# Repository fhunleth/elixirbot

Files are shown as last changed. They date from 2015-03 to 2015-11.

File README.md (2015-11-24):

# ElixirBot

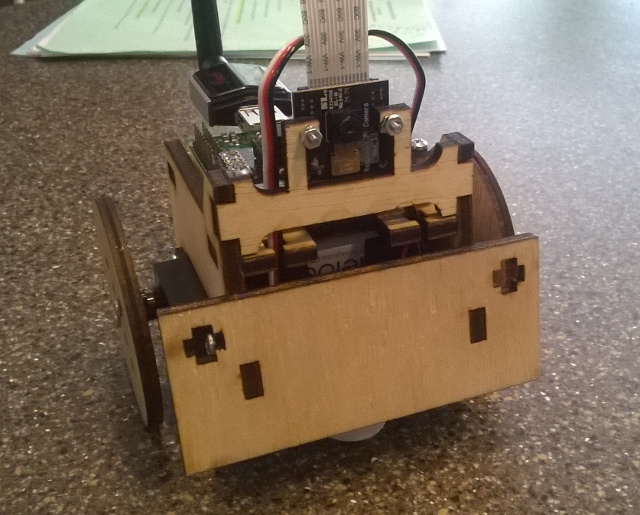
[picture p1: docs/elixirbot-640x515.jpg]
ElixirBot!!!


## Parts

The following lists all of the parts except for the laser cut frame and 3D
printed ball bearing holder. If you have a local hackerspace or Fab Lab, you're
in luck. If not, companies like Pololu and Ponoko will do it for you, but I have
not tested the designs with either of them.

  - Raspberry Pi Model A+ - $20
  - Pi Camera - $30
  - 2 [Spring RC SM-S4303R Servos](https://www.pololu.com/product/1248) - $26
  - WiFi dongle
  - [Daughter board PCB](https://oshpark.com/shared_projects/lCHfJqx6) - $3
  - [Pololu 5V Step-Up/Step-Down Voltage Regulator S7V7F5](https://www.pololu.com/product/2119) - $5
  - [4-AA Battery Holder](https://www.pololu.com/product/1153) - $1
  - [8-pin DIP socket](http://www.digikey.com/product-detail/en/A08-LC-TT/AE9986-ND/821740)
  - [10 position socket](http://www.digikey.com/product-detail/en/61301021821/732-2861-ND/2508630)
  - [2 position, 2.54 mm terminal block](http://www.digikey.com/product-detail/en/OSTVN02A150/ED10561-ND/1588862)
  - [ATtiny85](http://www.digikey.com/product-detail/en/ATTINY85-20PU/ATTINY85-20PU-ND/735469) - $2
  - [16 mm ball bearing](http://www.mcmaster.com/#9292k53/=w80vpw) - $1
  - [3/8" #6 pan head screws](http://www.mcmaster.com/#90190a146/=w80x6q)
  - [3/8" #4 pan head screws](http://www.mcmaster.com/#90190a103/=w80y2f)
  - [7/16" 4-40 F-F standoffs](https://www.pololu.com/category/114/female-female-standoffs)
  - [5/16" 4-40 machine screws](https://www.pololu.com/product/1961)
  - [4-40 machine hex nuts](https://www.pololu.com/product/1068)
  - [2-56 machine hex nuts](https://www.pololu.com/product/1067)
  - [5/16" 2-56 machine screws](https://www.pololu.com/product/1956)
  - [.1" header header]()
  - [.1" short]()
  - [10K resister 0805 package]()
  - [.1 uF capacitor 0805 package]()
  - MicroSD card
  - Rechargable AA batteries - Eneloop or other ~2000 mAh batteries

Very useful items:

  - [3V FTDI cable](https://www.sparkfun.com/products/9717)

## Building the frame

The robot frame is a modification of the awesome [SumoBot
Jr.](http://sumobotkit.com). I've made the following modifications to the
original design:

  1. Changed screw hole locations to mount a Raspberry Pi Model A
  2. Added a mount for a Pi Camera up front
  3. Added more room for batteries and enlarged the servo hole slightly
  4. Modified the wheels to screw into the servo horn rather than directly
     attaching (not completely sure that this is an improvement)

The `dxf` containing the laser cutter pattern was created in
[QCad](http://qcad.org). I cut the pattern in 5 mm birch plywood using a Full
Spectrum laser cutter. The Full Spectrum driver isn't smart about which lines to cut
first like the Epilog and Universal Laser drivers, so it has the cuts divided
into "first" and "second" passes.

## Building the electronics

First, order a PCB from [OSH Park](https://oshpark.com/shared_projects/lCHfJqx6).

IMPORTANT: I messed up the drill size for the 4-40 mounts, so the mounting holes
on the daughterboard need to be manually enlarged with a 7/64" drill bit. Don't
worry, I left clearance.

Solder the surface mount parts first. For the 10K resisters, make sure that you
have the orientation correct (same direction as silkscreen label). You'll see
what I mean.

The remaining components are fairly straightforward to solder since they're
through-hole. I didn't solder in the ISP connector, since I programmed the
ATtiny85 chips before plugging them into the board.

See the [ATtiny85 program](https://github.com/fhunleth/elixirbot/blob/master/hw/bot_attiny_controller/bot_attiny_controller.ino)
for build and programming instructions.

## Building

  1. Build a `nerves_rpi_elixirbot_defconfig` configuration of Nerves
  2. `. ./nerves-env.sh` in the Nerves directory
  3. Go here and run `make`

## Post-mortem

One thing I learned on this project was that the Raspberry Pi does not support
clock stretching on the I2C bus. Apparently, this was well documented, but I
hadn't seen it beforehand. The I2C code on the ATtiny85 does stretch the clock,
so if you rebuild this exactly, you will see I2C errors. With work, it may be
possible to fix the clock stretching issue, but if I were to do this project
again, I would look at another part besides the ATtiny85 or see if the RPi's PWM
support is improved.

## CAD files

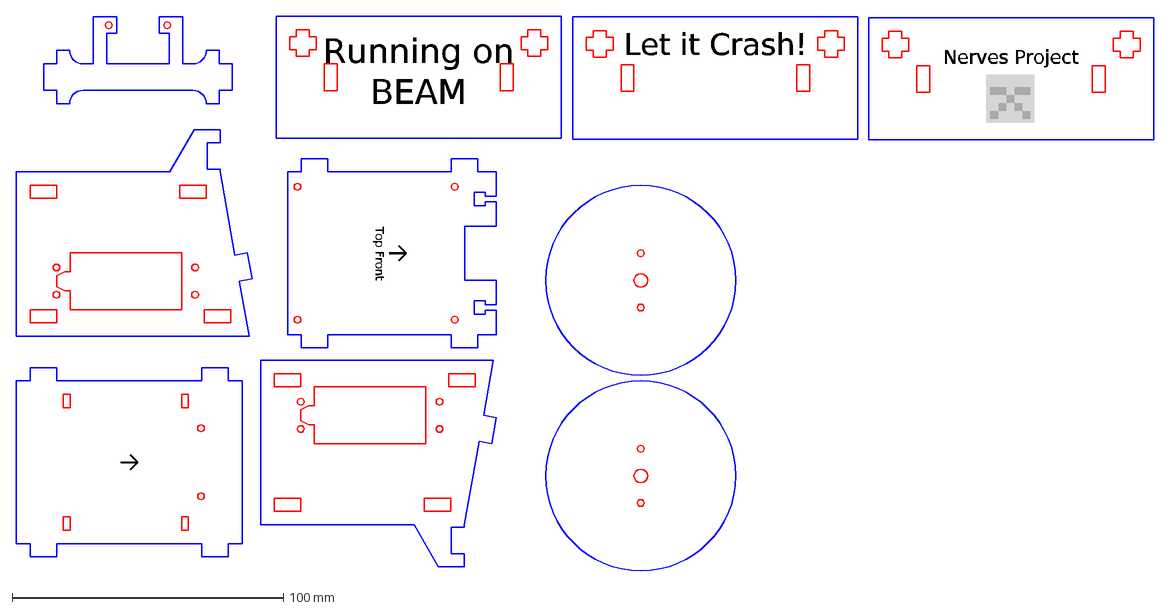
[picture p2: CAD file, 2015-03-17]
hw/PiSumoBot.dxf
Top Front
Running on BEAM
Let it Crash!
Nerves Project

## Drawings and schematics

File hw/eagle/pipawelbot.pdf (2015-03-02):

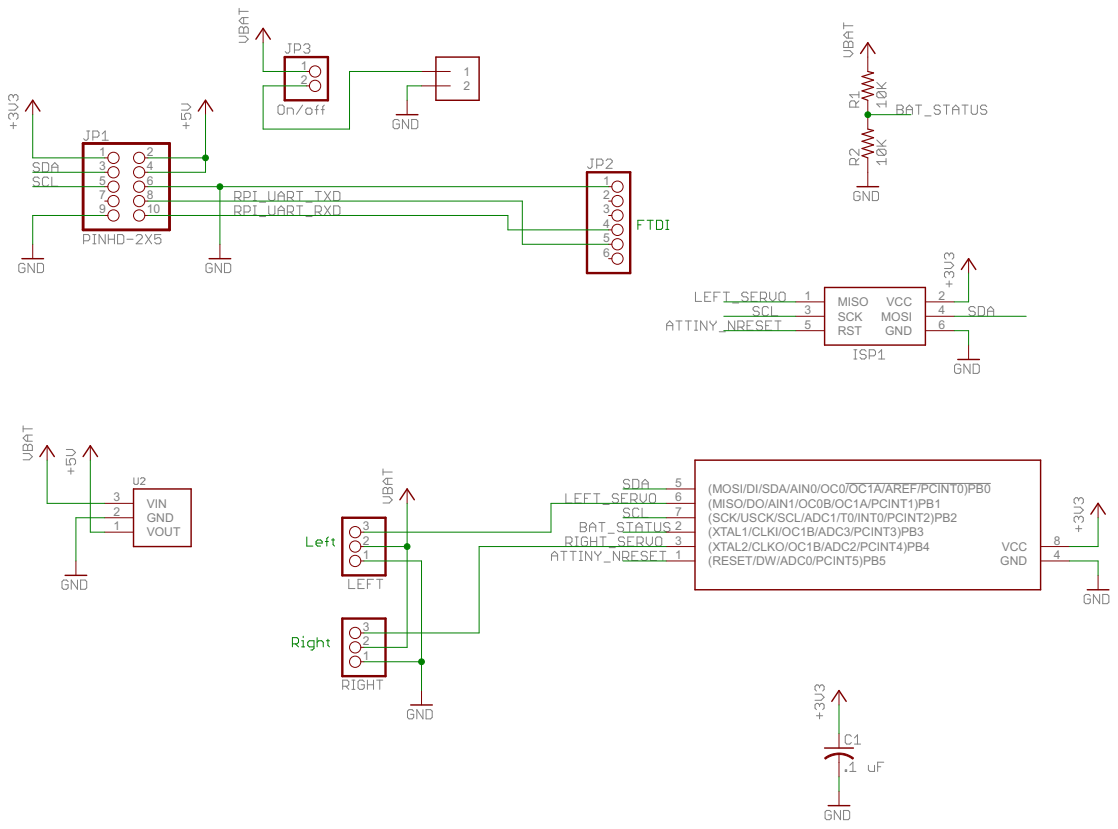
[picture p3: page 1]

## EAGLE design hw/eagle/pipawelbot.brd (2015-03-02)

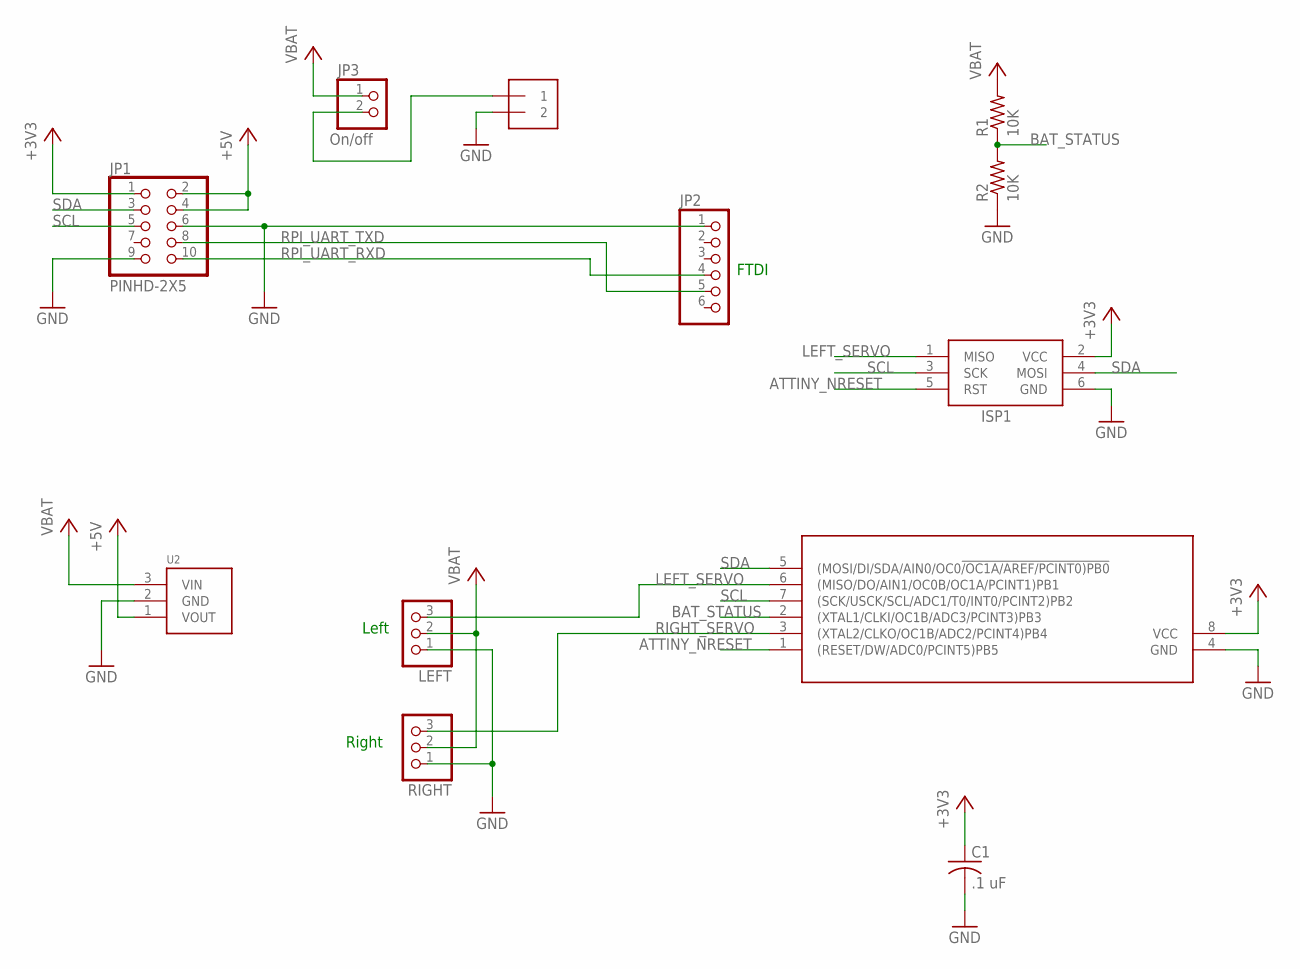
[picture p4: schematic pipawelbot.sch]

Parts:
C1: .1 uF; C0805
ISP1: AVRISP-6; AVRISP
J1: TERMINAL_BLOCK_1X2-2.54MM; TERMINAL_BLOCK-1X2-0.1
JP1: PINHD-2X5; 2X5
JP2: PINHD-1X6; 1X06
JP3: PINHD-1X2; 1X02
LEFT: PINHD-1X3; 1X03
R1, R2: 10K; R0805
RIGHT: PINHD-1X3; 1X03
U1: ATTINY85; DIL08
U2: S7V7F5; POLOLU-REG

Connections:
+3V3: C1.1, ISP1.2 (VCC), JP1.1, U1.8 (VCC)
+5V: JP1.2, JP1.4, U2.1 (VOUT)
ATTINY_NRESET: ISP1.5 (RST), U1.1 ((RESET/DW/ADC0/PCINT5)PB5)
BAT_STATUS: R1.1, R2.2, U1.2 ((XTAL1/CLKI/OC1B/ADC3/PCINT3)PB3)
GND: C1.2, ISP1.6 (GND), J1.1 (2), JP1.6, JP1.9, JP2.1, LEFT.1, R2.1, RIGHT.1, U1.4 (GND), U2.2 (GND)
LEFT_SERVO: ISP1.1 (MISO), LEFT.3, U1.6 ((MISO/DO/AIN1/OC0B/OC1A/PCINT1)PB1)
RIGHT_SERVO: RIGHT.3, U1.3 ((XTAL2/CLKO/OC1B/ADC2/PCINT4)PB4)
RPI_UART_RXD: JP1.10, JP2.4
RPI_UART_TXD: JP1.8, JP2.5
SCL: ISP1.3 (SCK), JP1.5, U1.7 ((SCK/USCK/SCL/ADC1/T0/INT0/PCINT2)PB2)
SDA: ISP1.4 (MOSI), JP1.3, U1.5 ((MOSI/DI/SDA/AIN0/OC0!/OC1A/AREF/PCINT0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)
VBAT_IN: J1.2 (1), JP3.2
VCC: JP3.1, LEFT.2, R1.2, RIGHT.2, U2.3 (VIN)

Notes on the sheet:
Left
Right
FTDI
On/off

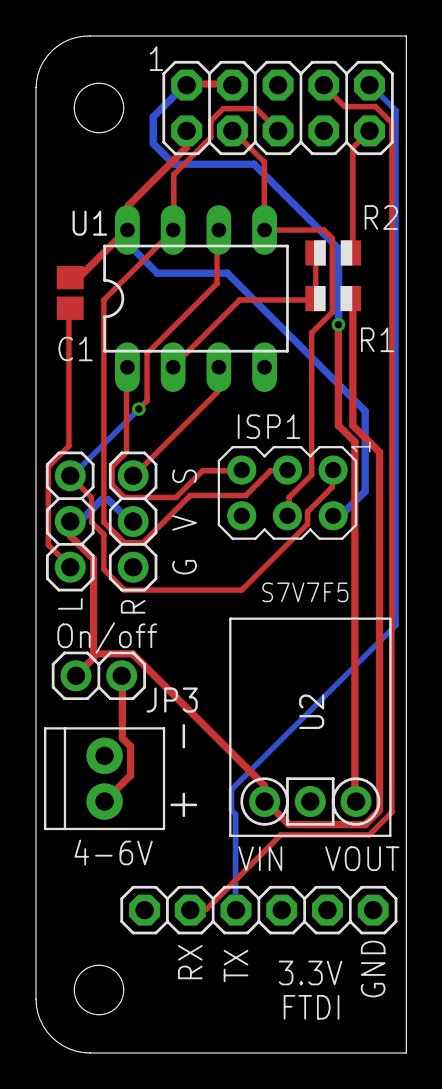
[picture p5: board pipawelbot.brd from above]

Board: 2 copper layers, 20.6 x 56.5 mm, 12 parts (0 on the bottom side), 13 nets.

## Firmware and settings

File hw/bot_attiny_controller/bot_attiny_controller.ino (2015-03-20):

/**
 * PawelBot servo controller for the Raspberry Pi.
 *
 * This program runs on an ATtiny85 connected to the RPi via the
 * I2C lines. It generates the PWM signals needed to control two
 * continuous turn servos. It also has an ADC input for checking
 * the battery level.
 *
 * To test on Raspian:
 *
 * Connect the ATtiny85's I2C pins to the I2C pins on the
 * Raspberry Pi's GPIO connector
 *
 * # sudo apt-get install i2c-tools
 * # sudo raspi-config
 * In raspi-config, enable I2C through the advanced menu.
 *
 * # sudo modprobe i2c-dev
 * # sudo i2cdetect -y 1
 *      0  1  2  3  4  5  6  7  8  9  a  b  c  d  e  f
 * 00:          -- 04 -- -- -- -- -- -- -- -- -- -- --
 * 10: -- -- -- -- -- -- -- -- -- -- -- -- -- -- -- --
 * 20: -- -- -- -- -- -- -- -- -- -- -- -- -- -- -- --
 * 30: -- -- -- -- -- -- -- -- -- -- -- -- -- -- -- --
 * 40: -- -- -- -- -- -- -- -- -- -- -- -- -- -- -- --
 * 50: -- -- -- -- -- -- -- -- -- -- -- -- -- -- -- --
 * 60: -- -- -- -- -- -- -- -- -- -- -- -- -- -- -- --
 * 70: -- -- -- -- -- -- -- --
 *
 * If the device doesn't show up (i.e. the 04), then
 * check the connections.
 *
 * # sudo i2cget -y 1 4 0 w    ## get left servo pulse duration
 * 0x05dc                      ## 0x05dc = 1500 microsecond pulse
 *
 * # sudo i2cget -y 1 4 2 w    ## get right servopulse duration
 * 0x05dc
 *
 * # sudo i2cget -y 1 4 4 w    ## get battery voltage
 * 0x138e                      ## 0x138e = 5006 microVolts
 *
 * # sudo i2cset -y 1 4 0 1200 ## set the left servo pulse to 1200 us
 * # sudo i2cset -y 1 4 2 1500 ## set the right right pulse to 1500 us
 *
 * *** There are intermittent I2C failures. I have not tracked them down. ***
 *
 * Programming an ATtiny85 with an Arduino Uno
 *
 * 1. Untar tiny.tgz into your ~/sketchbook/hardware or whereever your
 *    Arduino sketchbook directory is. These files come from http://hlt.media.mit.edu/?p=1229,
 *    but they're not always available. As a bonus, I've already made
 *    a boards.txt that defines the right ATtiny85 configuration for this project.
 * 2. In ~/sketchbook/libraries, run:
 *       git clone https://github.com/rambo/TinyWire.git
 * 3. Restart the Arduino IDE if you have it open, so that it finds the TinyWireS library
 * 4. In the Arduino IDE, program the ArduinoISP firmware onto the Uno
 *    (it's an example Arduino program)
 * 5. In Arduino IDE, set the board to "ATtiny85 @ 8 MHz (internal oscillator; BOD disabled)
 * 6. Set the programmer to "Arduino as ISP"
 *
 *  -- Setup steps are done --
 *
 * 7. Wire the Uno to the ATtiny85 like this:
 *      Arduino +5V    ---> ATtiny Pin 8
 *      Arduino Ground ---> ATtiny Pin 4
 *      Arduino Pin 10 ---> ATtiny Pin 1
 *      Arduino Pin 11 ---> ATtiny Pin 5
 *      Arduino Pin 12 ---> ATtiny Pin 6
 *      Arduino Pin 13 ---> ATtiny Pin 7
 *      Arduino Reset, Arduino group -> connect with 10 uF capacitor
 * 8. Burn bootloader (VERY, VERY IMPORTANT. I learned the hard way.)
 * 9. Compile and upload this program.
 */


/**
 * ATtiny85 pin assignments
 *
 * Pin   Function
 * 1     NRESET
 * 2     PB3 - Battery level/2 * 3.3/255
 * 3     PB4 - Right servo (OC1B)
 * 4     GND
 * 5     PB0 - I2C SDA
 * 6     PB1 - Left servo (OC1A)
 * 7     PB2 - I2C SCL
 * 8     VCC (+3.3V)
 */

#define I2C_SLAVE_ADDRESS 0x4
#include <TinyWireS.h>

enum I2cRegisters {
    I2cRegLeftServoLo = 0,
    I2cRegLeftServoHi,
    I2cRegRightServoLo,
    I2cRegRightServoHi,
    I2cRegBatteryLo,
    I2cRegBatteryHi,
    I2cRegReadRequestCount,
    I2cRegWriteRequestCount,
    I2cRegCount
};

static volatile uint8_t currentRegister = 0;

static uint16_t leftServoMicros = 1500;
static uint16_t rightServoMicros = 1500;
static uint16_t batteryMicroVolts = 0;
static uint8_t readRequestCount = 0;
static uint8_t writeRequestCount = 0;

#if F_CPU == 8000000L
// Divide FCLK by 64 -> 8 MHz/64 = 125 KHz (each tick is 8 uS)
#define TCCR1_CS_BITS 0x7
#else
#error Unexpected CPU speed
#endif

/*
 * Handle a 'get' request from the I2C master.
 */
void requestEvent()
{
    readRequestCount++;

    byte value;
    switch (currentRegister) {
    case I2cRegLeftServoLo:
        value = lowByte(leftServoMicros);
        break;
    case I2cRegLeftServoHi:
        value = highByte(leftServoMicros);
        break;
    case I2cRegRightServoLo:
        value = lowByte(rightServoMicros);
        break;
    case I2cRegRightServoHi:
        value = highByte(rightServoMicros);
        break;
    case I2cRegBatteryLo:
        value = lowByte(batteryMicroVolts);
        break;
    case I2cRegBatteryHi:
        value = highByte(batteryMicroVolts);
        break;
    case I2cRegReadRequestCount:
        value = readRequestCount;
        break;
    case I2cRegWriteRequestCount:
        value = writeRequestCount;
        break;
    default:
        value = 0;
        break;
    }
    TinyWireS.send(value);
    currentRegister++;
    if (currentRegister >= I2cRegCount)
        currentRegister = 0;
}

/*
 * Remove everything in the receive buffer.
 * This is usually called in case of error
 * where we're not quite sure what the user
 * was doing or whether there was an error.
 */
static void flushReceiveBuffer()
{
    while (TinyWireS.available())
        TinyWireS.receive();
}

/*
 * Handle a 'set' request from the I2C master.
 */
void receiveEvent(uint8_t howMany)
{
    static uint16_t nextLeftServoMicros = 0;
    static uint16_t nextRightServoMicros = 0;

    // Sanity check
    if (howMany < 1 || howMany > I2cRegCount) {
        flushReceiveBuffer();
        return;
    }

    // Read register position
    currentRegister = TinyWireS.receive();
    howMany--;
    writeRequestCount++;

    if (currentRegister >= I2cRegCount) {
        // If invalid register, ignore the request
        currentRegister = 0;
        flushReceiveBuffer();

        // Idle the servos since we're confused
        // This is mostly for debug.
        leftServoMicros = 1500;
        rightServoMicros = 1500;
        return;
    }

    // If any bytes left, write them to registers
    while (howMany) {
        byte value = TinyWireS.receive();
        howMany--;
        switch (currentRegister) {
        case I2cRegLeftServoLo:
            nextLeftServoMicros = (nextLeftServoMicros & 0xff00) | value;
            break;
        case I2cRegLeftServoHi:
            nextLeftServoMicros = (nextLeftServoMicros & 0x00ff) | (value << 8);
            break;
        case I2cRegRightServoLo:
            nextRightServoMicros = (nextRightServoMicros & 0xff00) | value;
            break;
        case I2cRegRightServoHi:
            nextRightServoMicros = (nextRightServoMicros & 0x00ff) | (value << 8);
            break;
        default:
            break;
        }
        currentRegister++;
        if (currentRegister >= I2cRegCount)
            currentRegister = 0;
    }
    writeRequestCount += howMany;

    if (nextLeftServoMicros >= 1000 && nextLeftServoMicros <= 2000)
        leftServoMicros = nextLeftServoMicros;

    if (nextRightServoMicros >= 1000 && nextRightServoMicros <= 2000)
        rightServoMicros = nextRightServoMicros;
}

void setup()
{
    // Servos like PWM durations around 1.5 ms with periods of 15-20 ms
    // The important part is the duration.

    // Since the ATtiny85 only has an 8 bit PWM, there's not enough precision
    // to just use a PWM (aka Timer/Counter). To see this, we'd like to get
    // 180 or more steps between 1-2 ms (so that we can do 0-180 degrees with
    // 1 degree resolution). This requires about 5 uS resolution. To get to
    // 20 ms would require counting to 4000, and that's not considering that
    // the ATtiny85 can't be set to count at any frequency.

    // What we do instead is send a pulse using Timer/Counter1 and then busy
    // wait between pulses. The busy wait doesn't need to be perfect, so if
    // I2C handling delays things a little, that's ok.

    pinMode(1, OUTPUT); // Left servo
    pinMode(4, OUTPUT); // Right servo
    pinMode(3, INPUT);  // Battery level

    /**
     * Reminder: taking care of pull-ups is the masters job
     */
    TinyWireS.begin(I2C_SLAVE_ADDRESS);
    TinyWireS.onReceive(receiveEvent);
    TinyWireS.onRequest(requestEvent);
}

uint8_t mapServoMicros(uint16_t micros)
{
    return (uint8_t) (uint32_t(micros - 16) * 254 / 2032) + 1;
}

void loop()
{
    // Our target is around 20 ms between pulses, so wait for 19 ms
    // between pulses to give time for ADC read and calculations.
    tws_delay(19); // Can't call delay() due to TinyWireS limitation

    // Sample the battery voltage (this takes about 100 microseconds according to docs)
    // The battery voltage is halved by a resister divider so that 6 V is
    // less that the 3.3 V reference voltage.
    batteryMicroVolts = (uint16_t) (uint32_t(analogRead(3)) * 2 * 3300 / 1023); // 6600 microvolts at 1023 counts

    // Start the counter over from 0 (Have to do this first to avoid spurious pulse since
    // there's no stopping the timer/counter)
    TCNT1 = 0;

    // Calculate the new pulse durations
    // This calculation takes more than a few microseconds, so will need to restart the
    // TCNT1 to accurately measure the duration
    OCR1A = mapServoMicros(leftServoMicros);
    OCR1B = mapServoMicros(rightServoMicros);

    // Force both outputs high.
    // The way this is done is by telling the Timer/Counter to set the outputs
    // high on match and then artificially trigger a match.
    // NOTE: You can't just set the output high since the Timer/Counter is now
    //       controlling it.
    TCCR1 = (1 << COM1A1) | (1 << COM1A0) | TCCR1_CS_BITS;
    GTCCR = (1 << COM1B1) | (1 << COM1B0) | (1 << FOC1B) | (1 << FOC1A);

    // Start the counter counting for real now that the outputs are officially high
    TCNT1 = 0;

    // Tell the Timer/Counter to set the outputs low on match (a real match this time)
    GTCCR = (1 << COM1B1) | (0 << COM1B0);
    TCCR1 = (1 << COM1A1) | (0 << COM1A0) | TCCR1_CS_BITS;
}

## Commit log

2015-02-28 Direction fixes for weird servo
2015-02-28 Add laser cut outlines
    [PiSumoBot.dxf]
2015-03-02 Add Eagle files for daughterboard
    [pipawelbot.brd, pipawelbot.sch]
2015-03-08 Add lots more instructions, BOM, and cleanup
2015-03-17 Latest updates to laser cut images
    Cuts well on 45W Full Spectrum Laser on 5mm plywood
    [PiSumoBot.dxf]
2015-03-17 Remove overlapping lines on camera holder
    [PiSumoBot.dxf]
